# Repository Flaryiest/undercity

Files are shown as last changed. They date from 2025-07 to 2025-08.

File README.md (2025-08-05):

Do you like Squid Game!!!

Sample Assembly
https://www.youtube.com/shorts/GGOR0AeZYXc  
  
This project is a flywheel disc shooter mounted on a turret platform with motion detection, simulating the "Red Light, Green Light" game in Squid Game.  

firefox_qANK9je56S
Discord_66T32WqUX3

We made a few unique design choices while CADing and programming the launcher.
- Our launching mechanism involved a single motor-powered flywheel (contrary to the usual 2 due to materials constraints) which would accelerate a plastic disc as it passed in front of the wheel:

 

- To sustain a more continuous rate of fire, we used a gravity-fed hopper design, in which the discs slowly fall into the barrel and are pushed into the flywheel:
  

- To generate linear motion for the disc pusher, we used a rack and pinion setup, with the rack built into the pushing block and the pinion being powered by a mini servo:

  

- To combat the load of the battery and motor on the turret platform, we geared the stepper motor in a 1:2 ratio:
  

Unfortunately, the turret platform did not print in time, and our robot cannot turn around, so we decided to scale down the project and focus on the launcher mechanism.

If there is motion directly in front of the launcher, the launcher fires, sort of like a sentry watching a set sightline.

## Firmware  
The code is done on a combination of a orpheus pico and a computer. The computer does the motion detection and depth tracking in motionDetection.py, using opencv and MiDaS. From there, it sends commands to the pico which then runs the motor and servo.  
The orpheus pico and electronics use circuit python, and relies on the adafruit motor library.  
motion detection:  https://www.youtube.com/shorts/whcpX-JFEPc

To run the code:  
- Download circuit python on your raspberry/orpheus pico  
- Add the adafruit motor library to the library folder of your MCU  
- Clone this repository  
- Run goodCode/motionDetection.py  

## Bill of Materials (BOM)

| Quantity | Item | Link |
|---|---|---|
| 14 | 3D Printed Parts | (Lots of filament) |
| 1 | Webcam | [FWV Streaming Webcam](https://www.amazon.com/FWV-Streaming-Microphone-Desktop-Studying/dp/B0D72VQR6Q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) |
| 1 | 550 Motor | [REV Robotics 550 Motor](https://www.revrobotics.com/rev-21-1651/?gQT=2) |
| 1 | 7.4V 2S Battery | [Zeee 7.4V Battery](https://www.amazon.com/Zeee-Batteries-Dean-Style-Connector-Vehicles/dp/B076Z778MJ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) |
| 1 | Stepper Motor | [STEPPERONLINE Bipolar Stepper](https://www.amazon.com/STEPPERONLINE-Stepper-Bipolar-Connector-compatible/dp/B00PNEQKC0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) |
| 1 | Stepper Motor Driver (A4988) | [Pololu A4988 Driver](https://www.pololu.com/product/1182) |
| 1 | Small Servo | [Micro Servo](https://www.amazon.com/Micro-Servos-Helicopter-Airplane-Controls/dp/B07MLR1498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) |
| 1 | Orpheus Pico | [Raspberry Pi Pico](https://www.microcenter.com/product/661033/raspberry-pi-pico-microcontroller-development-board?rd=1) |
| 1 | Breadboard | [400-point Breadboard](https://www.amazon.com/BB400-Solderless-Plug-BreadBoard-tie-points/dp/B0040Z1ERO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) |

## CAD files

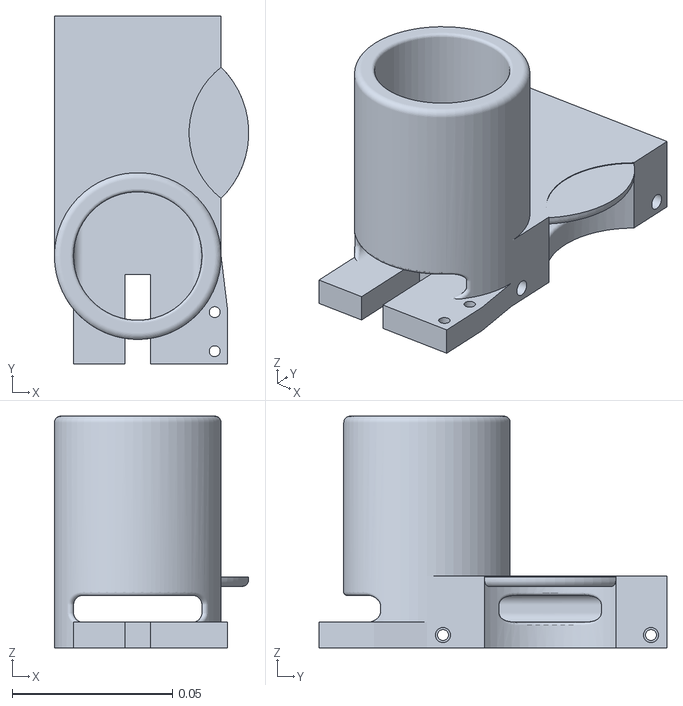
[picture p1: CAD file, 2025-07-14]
Production/Shooter Body.stl
0.0607 x 0.109 x 0.0724

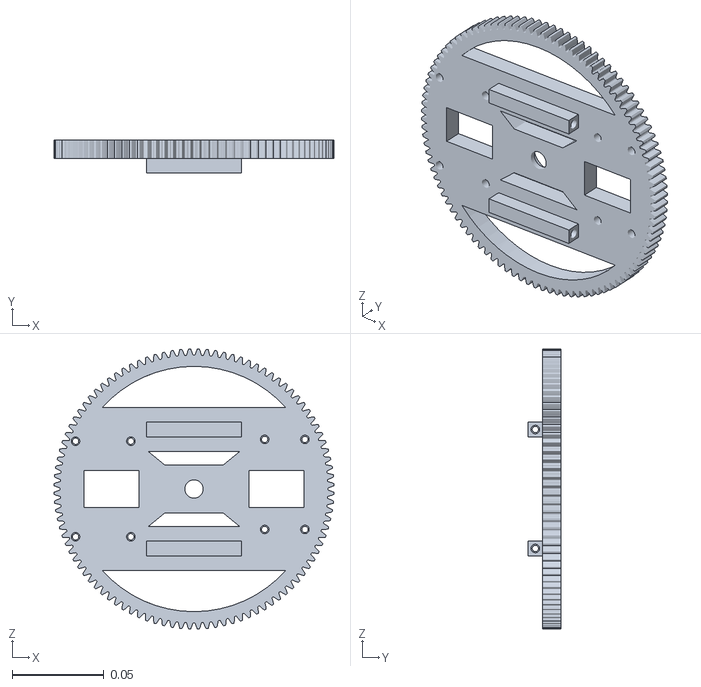
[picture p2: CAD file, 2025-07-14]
Production/Turret Platform.stl
0.153 x 0.018 x 0.153

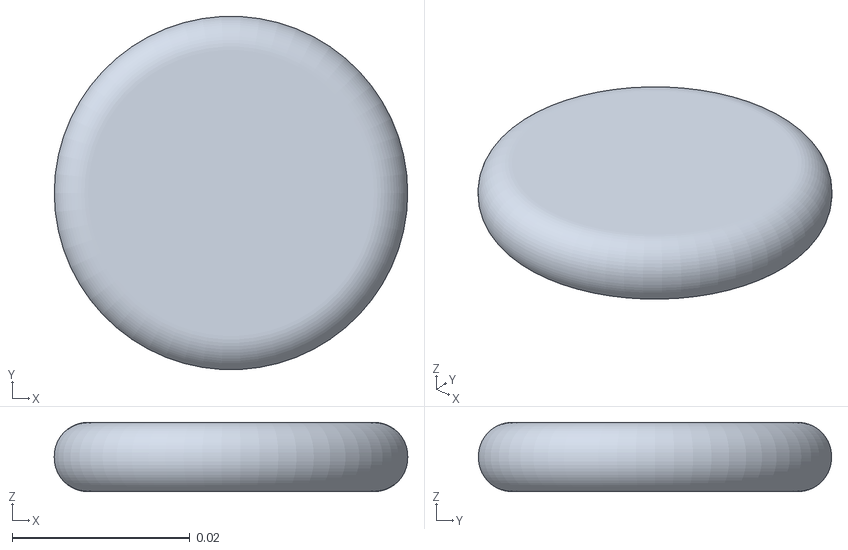
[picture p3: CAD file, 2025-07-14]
Production/Discs.stl
0.0398 x 0.0397 x 0.0078

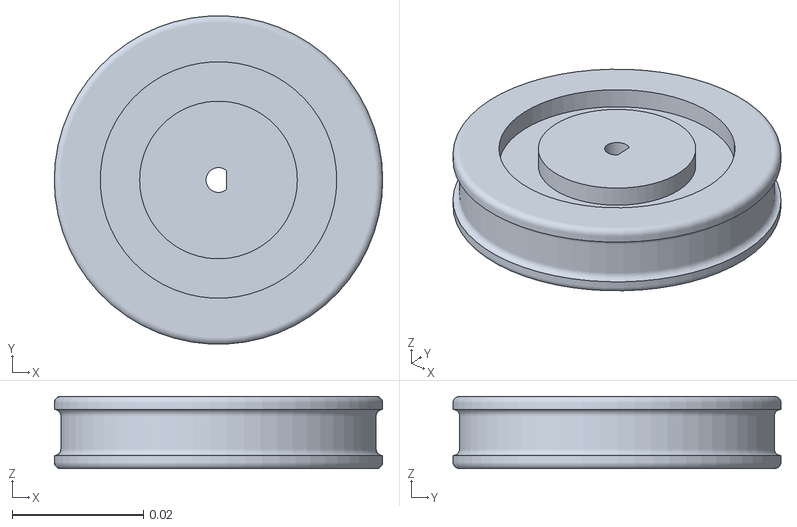
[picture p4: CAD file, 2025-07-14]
Production/Wheel.stl
0.05 x 0.0499 x 0.011

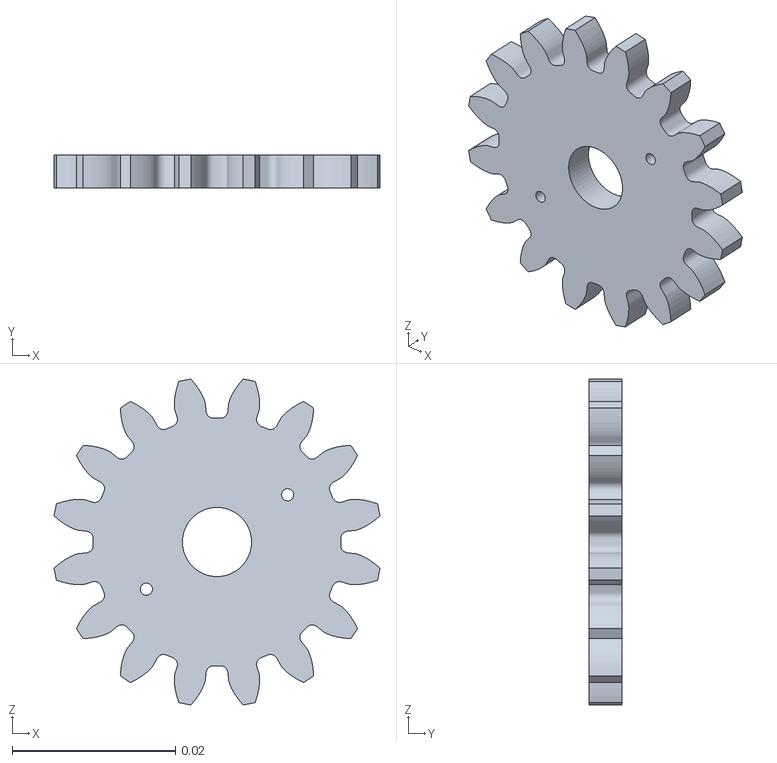
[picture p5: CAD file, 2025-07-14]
Production/Servo Gear.stl
0.04 x 0.004 x 0.04

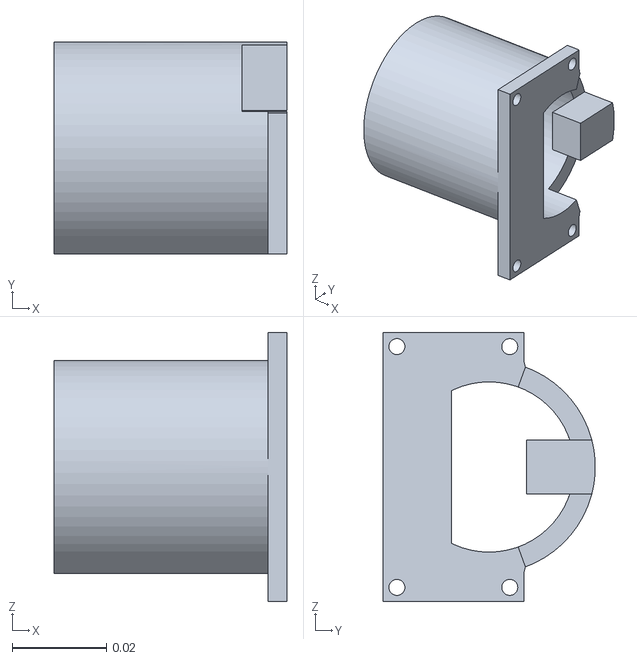
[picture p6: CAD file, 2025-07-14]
Production/Motor Mount.stl
0.0495 x 0.0452 x 0.0572

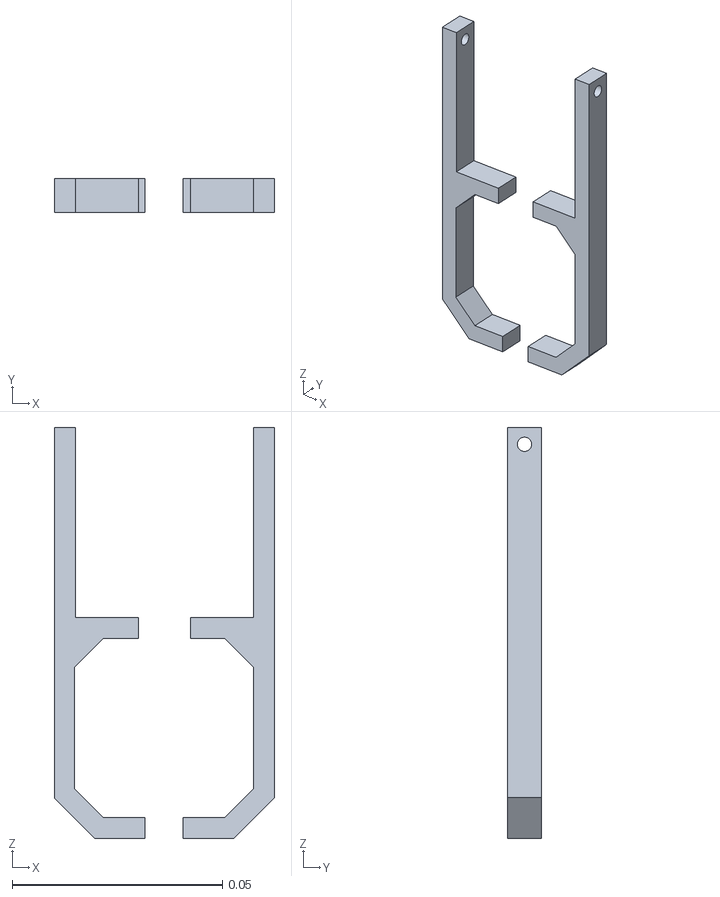
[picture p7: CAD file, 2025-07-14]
Production/Motor Connector.stl
0.0524 x 0.008 x 0.0978

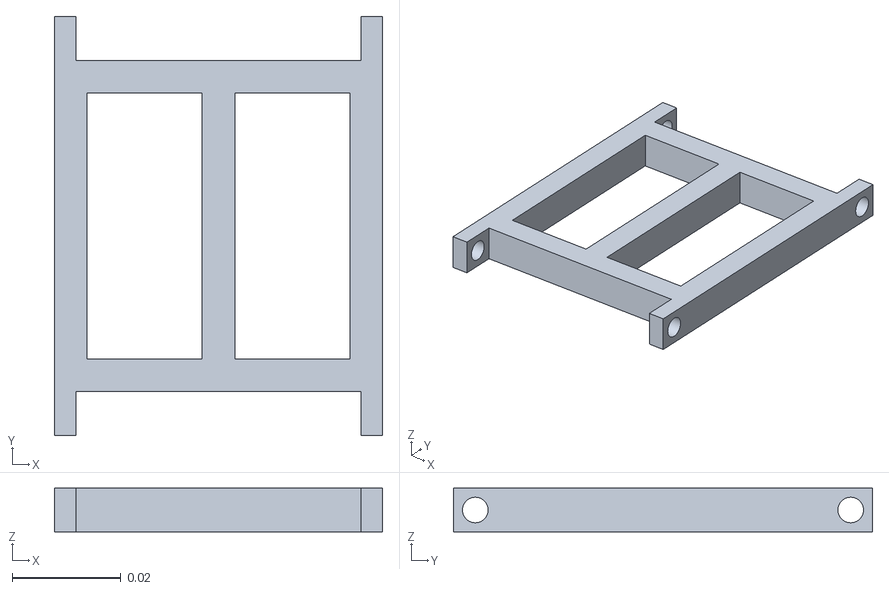
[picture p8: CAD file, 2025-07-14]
Production/Launcher Mounting.stl
0.0603 x 0.077 x 0.008

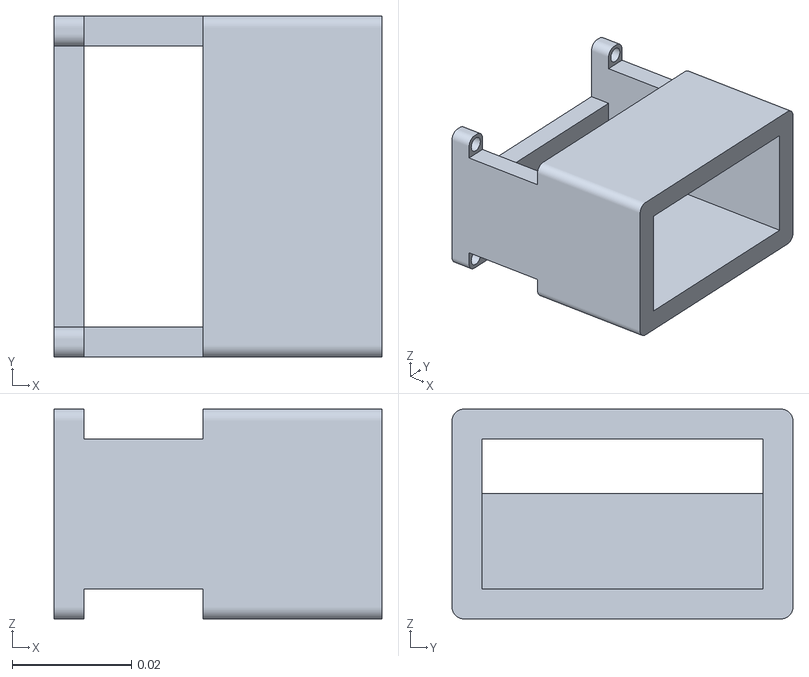
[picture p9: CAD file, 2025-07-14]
Production/Battery Mount.stl
0.055 x 0.0572 x 0.0352

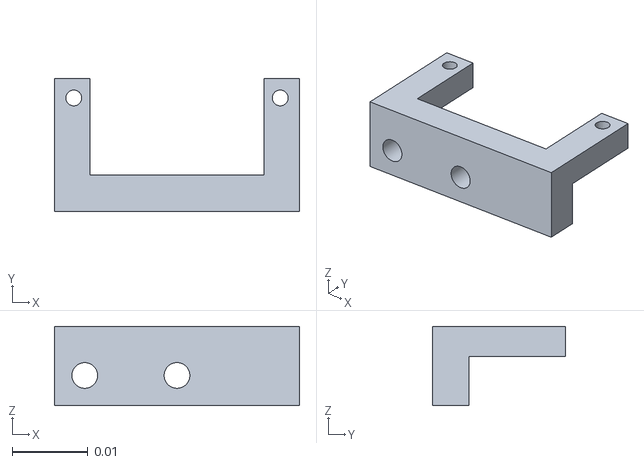
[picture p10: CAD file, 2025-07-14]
Production/Servo Mount.stl
0.0324 x 0.0175 x 0.0105

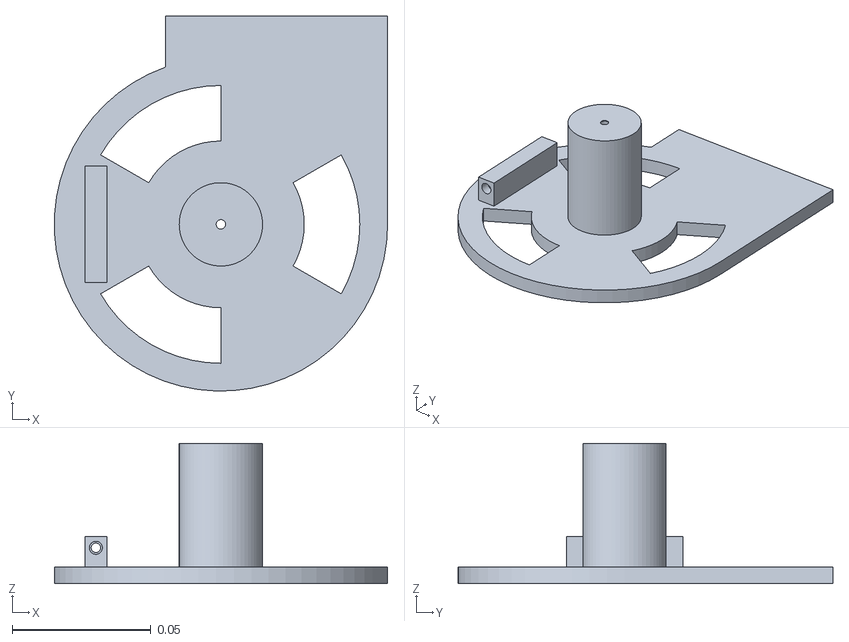
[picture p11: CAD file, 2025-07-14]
Production/Turret Base.stl
0.12 x 0.135 x 0.0505

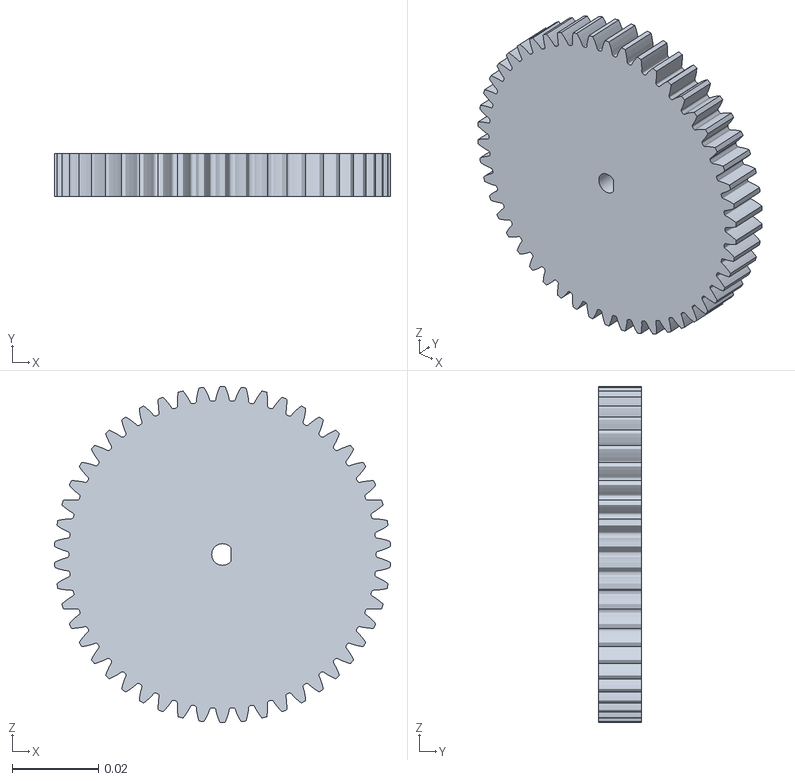
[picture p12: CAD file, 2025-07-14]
Production/Small Gear.stl
0.0779 x 0.01 x 0.078

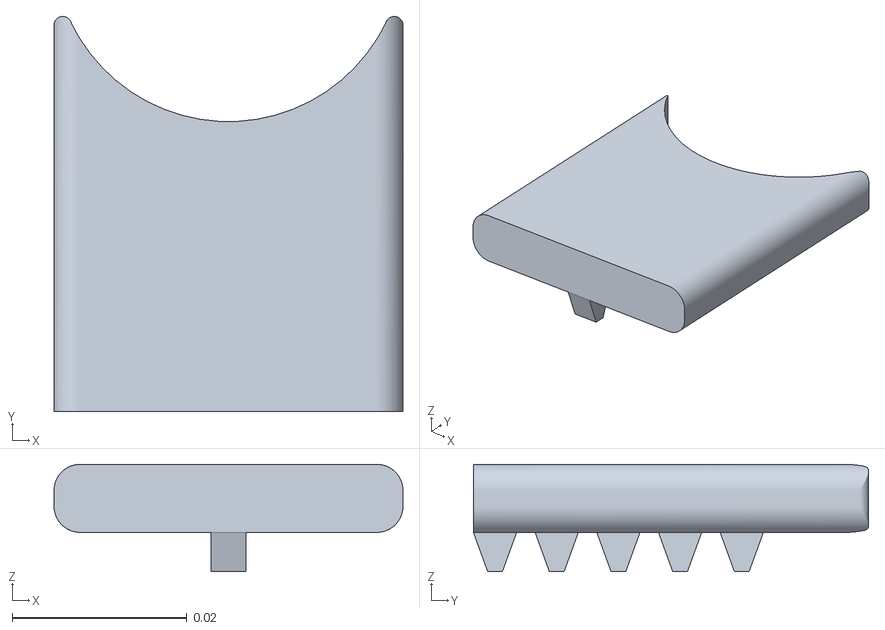
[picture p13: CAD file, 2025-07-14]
Production/Pusher Block.stl
0.04 x 0.0453 x 0.0123

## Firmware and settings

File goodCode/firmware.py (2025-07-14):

# Save as code.py on CIRCUITPY drive
import sys
import supervisor
import board
import digitalio
import pwmio
import time
from adafruit_motor import servo

# Initialize hardware
my_servo = None
brush_motor_available = False
esc_motor = None

# Declare stepper variables at module level
step_pin = None
dir_pin = None
stepper_motor = None

try:
    # Servo setup for Orpheus Pico - using GP0
    pwm = pwmio.PWMOut(board.GP0, duty_cycle=2 ** 15, frequency=50)
    my_servo = servo.Servo(pwm)
    print("Servo initialized on GP0 with 5V power")
except Exception as e:
    print(f"Servo init error: {e}")
    my_servo = None

try:
    # ESC setup for Orpheus Pico - using GP7
    esc_pwm = pwmio.PWMOut(board.GP7, duty_cycle=0, frequency=50)
    esc_motor = servo.ContinuousServo(esc_pwm)
    
    # Explicitly set to zero throttle
    esc_motor.throttle = 0.0
    time.sleep(0.5)
    
    print("ESC motor initialized on GP7")
    brush_motor_available = True
except Exception as e:
    print(f"ESC init error: {e}")
    brush_motor_available = False

try:
    # A4988 Stepper Driver setup using available pins GP11, GP12
    print("=== A4988 STEPPER MOTOR INITIALIZATION ===")
    print("Using GP11, GP12 for A4988 stepper driver")
    
    # Create digital pins for A4988 driver (STEP, DIR)
    step_pin = digitalio.DigitalInOut(board.GP11)
    dir_pin = digitalio.DigitalInOut(board.GP12)
    
    step_pin.direction = digitalio.Direction.OUTPUT
    dir_pin.direction = digitalio.Direction.OUTPUT
    
    step_pin.value = False
    dir_pin.value = False
    
    print("A4988 control pins initialized successfully")
    
    stepper_motor = "A4988_READY"  # Flag that stepper is ready
    
    print("A4988 STEPPER MOTOR - SUCCESS")
    
except Exception as e:
    print(f"A4988 stepper init error: {e}")
    stepper_motor = None
    step_pin = None
    dir_pin = None

def process_command(command):
    command = command.strip()
    
    if command == "library_test":
        return "Motor: True, Audio: True"
    
    elif command == "hardware_test":
        servo_status = "OK" if my_servo else "None"
        brush_status = "OK" if brush_motor_available else "None"
        stepper_status = "A4988_OK" if stepper_motor == "A4988_READY" else "None"
        return f"Servo: {servo_status}, Brush: {brush_status}, Stepper: {stepper_status}"
    
    elif command == "pin_test":
        available_pins = []
        in_use_pins = []
        test_pins = [f"GP{i}" for i in range(0, 29)]
        
        for pin_name in test_pins:
            try:
                pin = getattr(board, pin_name, None)
                if pin:
                    try:
                        test_pin = digitalio.DigitalInOut(pin)
                        test_pin.direction = digitalio.Direction.OUTPUT
                        available_pins.append(pin_name)
                        test_pin.deinit()
                    except Exception:
                        in_use_pins.append(pin_name)
            except:
                pass
        
        return f"Available: {', '.join(available_pins)} | In use: {', '.join(in_use_pins)}"
    
    elif command.startswith("servo:"):
        if my_servo:
            try:
                _, angle = command.split(":")
                target_angle = int(angle)
                print(f"Moving servo to {target_angle} degrees")
                my_servo.angle = target_angle
                time.sleep(0.5)
                return f"Servo moved to {target_angle} degrees"
            except Exception as e:
                print(f"Servo command error: {e}")
                return f"Servo error: {e}"
        else:
            return "Servo not available"

    elif command.startswith("stepper:"):
        if stepper_motor == "A4988_READY" and step_pin and dir_pin:
            try:
                _, steps_str = command.split(":")
                steps = int(steps_str)
                print(f"Moving A4988 stepper {steps} steps")
                
                # Set direction (True = forward, False = backward)
                dir_pin.value = steps > 0
                abs_steps = abs(steps)
                
                # Generate step pulses
                for i in range(abs_steps):
                    step_pin.value = True
                    time.sleep(0.001)  # 1ms pulse width
                    step_pin.value = False
                    time.sleep(0.01)   # 10ms between steps (100 steps/second)
                
                return f"A4988 moved {steps} steps"
            except Exception as e:
                print(f"A4988 command error: {e}")
                return f"A4988 error: {e}"
        else:
            return "A4988 stepper not available"

    elif command == "stepperTest":
        if stepper_motor == "A4988_READY" and step_pin and dir_pin:
            try:
                print("Testing A4988 stepper - 50 steps forward, 50 steps back")
                
                # 50 steps forward
                dir_pin.value = True
                for i in range(50):
                    step_pin.value = True
                    time.sleep(0.001)
                    step_pin.value = False
                    time.sleep(0.02)  # Slower for test
                
                time.sleep(0.5)  # Pause between directions
                
                # 50 steps backward
                dir_pin.value = False
                for i in range(50):
                    step_pin.value = True
                    time.sleep(0.001)
                    step_pin.value = False
                    time.sleep(0.02)  # Slower for test
                
                return "A4988 test completed: 50 forward, 50 backward"
            except Exception as e:
                print(f"A4988 test error: {e}")
                return f"A4988 test error: {e}"
        else:
            return "A4988 stepper not available"

    elif command.startswith("brushMotor:"):
        if brush_motor_available:
            try:
                _, speed_str = command.split(":")
                speed = int(speed_str)
                throttle = speed / 100.0
                esc_motor.throttle = throttle
                
                if speed == 0:
                    return "Motor stopped"
                elif speed > 0:
                    return f"Motor forward at {speed}%"
                else:
                    return f"Motor reverse at {abs(speed)}%"
            except Exception as e:
                return f"Motor error: {e}"
        else:
            return "ESC not available"

    elif command == "servoThenMotor":
        if brush_motor_available and my_servo:
            try:
                print("Starting servo-then-motor sequence")
                
                # Move servo to 90 degrees first
                my_servo.angle = 90
                time.sleep(0.5)
                print("Servo moved to 90 degrees")
                
                # Run motor at 20% for 0.5 seconds
                esc_motor.throttle = 0.2
                time.sleep(0.5)
                esc_motor.throttle = 0.0
                print("Motor sequence completed")
                
                # Move servo back to 0
                my_servo.angle = 0
                time.sleep(0.5)
                print("Servo returned to 0 degrees")
                
                return "Servo-then-motor sequence completed"
            except Exception as e:
                print(f"Servo-then-motor error: {e}")
                return f"Servo-then-motor error: {e}"
        else:
            return "Servo or motor not available"

    elif command == "stepper_debug":
        if stepper_motor == "A4988_READY" and step_pin and dir_pin:
            try:
                print("A4988 Debug Test - Manual pin control")
                
                # Test direction pin
                print("Testing DIR pin - HIGH for 2 seconds")
                dir_pin.value = True
                time.sleep(2)
                
                print("Testing DIR pin - LOW for 2 seconds") 
                dir_pin.value = False
                time.sleep(2)
                
                # Test step pin with visible pulses
                print("Testing STEP pin - 10 slow pulses")
                for i in range(10):
                    print(f"Step pulse {i+1}")
                    step_pin.value = True
                    time.sleep(0.5)  # Long pulse so you can see it
                    step_pin.value = False
                    time.sleep(0.5)  # Long gap so you can see it
                
                return "A4988 debug test completed"
            except Exception as e:
                return f"Debug test error: {e}"
        else:
            return "A4988 not available for debug"

    else:
        return "Unknown command"

print("CircuitPython ready for commands")

while True:
    if supervisor.runtime.serial_bytes_available:
        try:
            cmd = sys.stdin.readline().strip()
            if cmd:
                result = process_command(cmd)
                if result:
                    print(result)
        except Exception as e:
            print(f"Error: {e}")

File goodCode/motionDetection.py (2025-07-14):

import cv2
import numpy as np
import time
import math
from music import CycleMusic, play_squid_music, stop_music
import torch
import torch.nn.functional as F
from torchvision.transforms import Compose
import urllib.request
import os
import serial
import serial.tools.list_ports

device = torch.device("cuda" if torch.cuda.is_available() else "cpu")

def find_xiao_port():
    ports = serial.tools.list_ports.comports()
    for port in ports:
        if "usbmodem" in port.device.lower() or "2e8a" in str(port.hwid):
            return port.device
    return None

try:
    PORT = find_xiao_port() or "/dev/cu.usbmodem11401"
    ser = serial.Serial(PORT, 115200, timeout=1)
    time.sleep(2)
    print(f"Connected to Xiao RP2040 on {PORT}")
    
    ser.write(b'\x03')
    time.sleep(0.5)
    ser.write(b'\x04')
    time.sleep(3)
    
    while ser.in_waiting > 0:
        ser.read(ser.in_waiting)
        time.sleep(0.1)
        
    motor_available = True
    print("Motor control ready")
except Exception as e:
    print(f"Motor connection failed: {e}")
    motor_available = False
    ser = None

def send_motor_command(cmd):
    """Send command to Xiao RP2040 and get response"""
    if not motor_available or ser is None:
        return "Motor not available"
    
    try:
        ser.write((cmd + "\r\n").encode("utf-8"))
        time.sleep(0.1)
        
        attempts = 0
        while attempts < 5:  # 0.5 second timeout
            if ser.in_waiting > 0:
                response = ser.readline().decode('utf-8', errors='ignore').strip()
                if response and not response.startswith('>>>') and response != cmd:
                    return response
            time.sleep(0.1)
            attempts += 1
        return "No response"
    except Exception as e:
        return f"Error: {e}"

def trigger_motor_and_servo():
    """Trigger servo first, then motor using combined command"""
    if motor_available:
        print("Motion detected! Running servo-then-motor sequence...")
        send_motor_command("servoThenMotor")
        print("Servo-then-motor sequence completed")

try:
    model_type = "MiDaS_small"
    midas = torch.hub.load("intel-isl/MiDaS", model_type, trust_repo=True)
    midas.to(device)
    midas.eval()
    
    midas_transforms = torch.hub.load("intel-isl/MiDaS", "transforms", trust_repo=True)
    transform = midas_transforms.small_transform
    print("MiDaS model loaded")
except Exception as e:
    print(f"Error loading MiDaS: {e}")
    midas = None
    transform = None

def estimate_depth(frame):
    if midas is None:
        return None
    
    try:
        rgb_frame = cv2.cvtColor(frame, cv2.COLOR_BGR2RGB)
        
        input_batch = transform(rgb_frame).to(device)
        
        with torch.no_grad():
            prediction = midas(input_batch)
            
            prediction = F.interpolate(
                prediction.unsqueeze(1),
                size=frame.shape[:2],
                mode="bicubic",
                align_corners=False,
            ).squeeze()
        
        depth_map = prediction.cpu().numpy()
        
        depth_normalized = cv2.normalize(depth_map, None, 0, 255, cv2.NORM_MINMAX, dtype=cv2.CV_8U)
        
        return depth_map, depth_normalized
    
    except Exception as e:
        print(f"Error in depth estimation: {e}")
        return None, None

def get_object_depth(depth_map, center_x, center_y, window_size=20):
    if depth_map is None:
        return None
    
    half_window = window_size // 2
    x_start = max(0, center_x - half_window)
    x_end = min(depth_map.shape[1], center_x + half_window)
    y_start = max(0, center_y - half_window)
    y_end = min(depth_map.shape[0], center_y + half_window)
    
    roi = depth_map[y_start:y_end, x_start:x_end]
    
    return np.median(roi)

cap = cv2.VideoCapture(0)

output_width = 1280
output_height = 720

fourcc = cv2.VideoWriter_fourcc(*'XVID')
out = cv2.VideoWriter('depth_motion_output.avi', fourcc, 20.0, (output_width, output_height))

# Create TWO separate background subtractors
background_subtractor_active = cv2.createBackgroundSubtractorMOG2(
    detectShadows=True,
    varThreshold=50,
    history=800
)

background_subtractor_pause = cv2.createBackgroundSubtractorMOG2(
    detectShadows=True,
    varThreshold=50,
    history=800
)

motion_threshold = 7000

print("Starting 60-second recording with AI depth estimation")
print("Motion detection cycles: OFF for first 6 seconds, then ON for 6 seconds")
print("Music: Squid music plays initially, then switches to green/red light cycling")
print("Press 'q' to quit early")

start_time = time.time()
recording_duration = 60  
cycle_duration = 6 

frame_center_x = output_width // 2
frame_center_y = output_height // 2

play_squid_music() 

cycle_music = CycleMusic(cycle_duration=6)
music_switched = False

depth_frame_skip = 5
frame_counter = 0
last_depth_map = None
last_depth_normalized = None

last_motion_trigger = 0
motion_cooldown = 2.0  # 2 seconds between triggers instead of 1.0
previous_detection_state = False
state_change_buffer_time = 2.0  
state_change_time = 0
contour_groups = []
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

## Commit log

2025-07-14 Create BOM
2025-07-14 Update BOM
2025-07-14 it's been 10 hours since I wrote this
    changed firmware to work for pico pins rather than xiao rp2040, fixed motion detection motor triggering
    [firmware.py, motionDetection.py]
2025-07-14 bom fixes
